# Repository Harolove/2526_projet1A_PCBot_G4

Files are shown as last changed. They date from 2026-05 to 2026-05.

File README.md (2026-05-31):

# 2526_projet1A_PCBot_G4
PCBot fait par le groupe de 4

## Rappels git

### Clé SSH

Dans git bash, lancez la commande suivante :

```bash
ssh-keygen
```

puis affichez la clé :

```bash
cat /c/Users/<USER>/.ssh/id_ed25519.pub
```

Créez une nouvelle clé dans github et collez la clé

### Clonez le projet

Pour récupérer le projet, à faire une fois (par projet).

```bash
git clone git@github.com:Harolove/2526_projet1A_PCBot_G4.git
```

### Faire un commit

A faire à chaque fois que quelque chose fonctionne, et après une séance de travail.

```bash
git status
git add .
git commit -m "Message"
git push
```

### Récupérer la dernière version

A faire à chaque fois qu'on commence à travailler

```bash
git pull
```
## Timeline
### 05/02/2026
Début du projet : Le professeur nous présente différents projets.
Nous avons choisi le PCBot car le projet nous paraît très intéressant même s'il en est un gros. Nous avons également utilisé cette séance pour découvrir git et github. Nous avons commencé les recherches des datasheets des différents composants du PCBot; et nous avons listé les différentes fonctionnalités de celui-ci.

### 12/02/2026
Draw.io :
- Schéma architectural

Kicad : 
- Début du schematic
- Modification des symboles déjà existants sur Kicad pour avoir des composants qui se rapprochent de ceux que nous allons utiliser

### 19/02/2026
Kicad :
- Création des feuilles hiérarchiques
- Continuation du schematic sur Kicad

### 12/03/2026
Kicad :
- Continuation du schematic sur Kicad

### 19/03/2026
Kicad : 
- Ajout de connexions inter-feuille
CubeIDE : 
- Début de code (détermination de position, calcul de distance avec obstacle, déplacement dans l'espace)

### 25/03/2026
Kicad :
- Début du routage (ajout des Mounting_Hole_Pad)
- Ajout des plans de masse (GND pour couches n°1, 2 et 4)

### 26/03/2026
CubeIDE :
- Modification du code et ajout de code test (car nous n'avons pas encore la carte)

### 09/04/2026
CubeIDE :
- Correction d'erreurs

### 16/04/2026
CubeIDE :
- Commentaire des différents fichiers .c et .h
- Recherche d'une librairie pour le capteur TOF

### 06/05/2026
Software : 
- Réussite à faire communiquer deux nRF24 avec deux Nucléos-L476RG

### 07/05/2026
Pratique :
- Soudure du PCB
Software :
- Test du code pour la centrale inertielle

### 13/05/2026
Pratique :
- Resoudure du PCB (car nous avons eu des problèmes la première fois)

### 15/05/2026
Software :
- Fonctionnement de la centrale inertielle

### 18/05/2026
Software :
- Test du code pour le capteur tof (mais n'a pas réussi à le faire fonctionner)
Onshape :
- Modélisation d'un support pour le PCB

### 19/05/2026
Onshape :
- Impression et assemblage du support

### Introduction:

Ce projet a pour objectif la conception d'un robot PCBot capable de connaître sa position dans l'espace et de se déplacer de manière autonome. Ce robot doit pouvoir cartographier un environnement en mesurant la distance qui le sépare des obstacles, et en communiquant avec d'autres PCBot, il peut reconstruire la carte d'un environnement beaucoup plus large.

### Choix des composants:

Nous avons choisi nos composants par rapport à trois critères: l'écologie, l'optimisation de l'espace et le coût.
- Pour la gestion de l'énergie, nous avons retenu le BMS BQ25896RTWR, qui accepte une large plage de tension d'entrée (3,9V à 14V) et offre un rendement supérieur à 90% à 3A, permettant l'utilisation d'adaptateurs standards (5V) ou haute tension (9V/12V).
- Pour le contrôle des moteurs DFR1224 à courant continu, nous avons opté pour le driver DRV8411APWPR pour sa compacité et sa simplicité d'utilisation, avec une large plage de fonctionnement de 1.65V à 11V.
- La localisation du robot repose sur la centrale inertielle LSM6DSOX, qui possède un accéléromètre et un gyroscope (que l'on n'utilisera pas dans le projet) dans un boîtier résistant aux chocs mécaniques.
- Pour la mesure de distance, nous avons choisi le capteur TOF VL53L0X pour ses bonnes performances en pleine lumière dans un encombrement réduit. 
- La communication sans fil entre robots est assurée par le module nRF24.

### Routage et conception du PCB:

Pour le routage, nous avons cherché à minimiser les distances entre composants interdépendants, en plaçant notamment les condensateurs de découplage au plus près des composants qu'ils protègent. Le PCB a été optimisé pour atteindre une taille minimale de 5,9 × 6,8 cm pour l'écologie.
Exemple: 



###

### Difficultés rencontrées:
Le soudage des composants a été l'étape la plus délicate du projet, marquée par plusieurs tentatives avant d'obtenir un résultat satisfaisant. Notre premier PCB a été un échec, car après le passage au four, nous avons remarqué que nous n’avons pas retiré la pâte à braser au niveau des trous du connecteur USB-C, rendant ainsi la carte inutilisable. Lors du deuxième essai, de la pâte à braser s’est retirée par inadvertance à certains endroits, compromettant là encore la qualité des soudures.
Sur notre PCB final, le passage au four a provoqué le déplacement de notre BMS et de certains condensateurs. De plus, une patte de la STM32 s’est pliée rompant ainsi le contact électrique avec plusieurs broches du microcontrôleur. Pour corriger ces problèmes, nous avons dû dessouder les composants concernés et les ressouder manuellement à l'air chaud avec du flux un liquide qui permet à l'étain de couler jusqu'aux pattes lors du chauffage à l'air chaud. Malgré ces difficultés, cette expérience nous a appris énormément sur les contraintes du soudage en production et sur les techniques de reprise manuelle. 

Après le soudage, nous avons tenté d'alimenter le PCB via un chargeur USB-C, mais les tensions mesurées au multimètre ne correspondaient pas aux valeurs attendues. Nous avons découvert que deux solder jumpers, JP1 et JP2, étaient ouverts par défaut, nous avons donc dû poser de l'étain dessus pour enfin avoir des alimentations correctes. Nous avons également constaté que le PCB ne fonctionnait qu'avec un chargeur USB-A, le chargeur USB-C ne semblant pas être reconnu correctement, sans que nous ayons pu en identifier la cause précise.

Du côté logiciel, nous n'avons pas réussi à établir la communication I2C avec le capteur TOF, que ce soit sur le PCB du projet ou avec notre STM32L476RG. Pourtant, la broche XSHUT a bien été mise à 1 dans le code, et l'alimentation du composant a été vérifiée avec un multimètre. 

### Modélisation 3D du support:
Nous avons conçu le support du robot sur OnShape. La principale contrainte de conception était d'assurer que les deux roues arrière et la bille aient la même hauteur pour garantir une surface de contact plane. Nous avons donc ajouté de la matière à l'avant du support afin de compenser la différence de hauteur.
Nous avons fait différents trous pour pouvoir faire rentrer les vis des moteurs et de la bille, et nous avons aussi fait le support pour le PCB. Cependant, l'impression n'a pas été parfaite et le support ne s'est pas emboîté correctement, pour pallier le problème, nous avons cassé l'un des picots du support afin que le PCB puisse tenir en place.





### IMU
Dans le cadre du projet, nous avons réalisé quelques tests avec le composant LSM6DSOX (Adafruit 4438), notre objectif était de pouvoir obtenir la distance parcourue par le composant à partir des données accélérométriques (par double intégration). Nous avons relié les lignes SDA et SCL de l’imu sur les broches PB6 et PB7 du microcontrôleur STM32L476RG.
Avant de faire ces tests, nous avons utilisé le registre WHO_AM_I du composant d’adresse 0x0F et qui contient 0x6C (108). Après lecture du contenu à cette adresse nous avons obtenu cette valeur, cela montre que le capteur est bien connecté.
Les registres OUTX et OUTY permettent de mesurer l'accélération selon l’axe x et l’axe y, cependant, dans le cadre de ces tests, nous allons plutôt nous concentrer sur un seul axe.
L'accélération est codée sur 16 bits au total, mais le bus I2C ne peut transférer que 8 bits à la fois. Donc le capteur découpe la valeur en deux morceaux de 8 bits et les range dans deux registres séparés :
- OUTX_L_A (0x28) contient les 8 bits de poids faible
- OUTX_H_A (0x29) contient les 8 bits de poids fort.



Le registre CTRL1_XL d’adresse 0x10 est le registre de configuration principal de l'accéléromètre. Il est composé de 8 bits répartis en trois parties :
- Les 4 bits de poids fort (ODR_XL3 à ODR_XL0) règlent la fréquence de mesure
- Les 2 bits suivants (FS1_XL, FS0_XL) règlent la plage de mesure
- Le bit LPF2_XL_EN active ou non un filtre passe-bas





Pour nos tests nous avons choisi d’envoyer 0x40 à ce registre qui correspond en binaire à 0100 0000, on a donc :
- 0100 pour ODR_XL qui correspond à 104 Hz dans le tableau pour un mode normal
- 00 pour FS_XL qui correspond à la plage ±2g (valeur par défaut)
- 00 pour le reste: filtre désactivé

On fixe la fréquence d'échantillonnage du capteur à 104 Hz, ce qui signifie qu'il prend 104 mesures par seconde, ce qui est largement suffisant pour nos tests, puisque dt = 0.02s correspond à une fréquence de 50 Hz dans le code. Le capteur mesure donc deux fois plus vite que notre boucle de calcul.
On fixe la plage à ±2g qui est adaptée pour nos tests car nos déplacements sont lents et à faible accélération.

L'approche que nous avons opté pour le code est d’implanter plusieurs variables volatiles:

- measurement_active: cette variable vaut 1 si la mesure est active et 0 sinon.
- pos_x: la position de x actuelle.
- x_pos_max: la position maximale de pox_x pendant une mesure, elle a été introduite car pos_x varie en continu et ne permet pas de lire directement une valeur stable.
  
Une mesure est lancée dès que l’on appuie sur le bouton poussoir PC13 et s’arrête lorsqu’on réappuie dessus pour nous donner la valeur de x_pos_max au cours de cette mesure. 

L'estimation de la position repose sur une double intégration temporelle. Cependant, cette intégration pose un problème de précision, de petites erreurs s'accumulent à chaque intégration et fausse le calcul de la position même quand le robot est immobile. Ainsi, pour limiter ces erreurs, nous avons mis en place 2 corrections:
- Les valeurs brutes du capteur sont converties en m/s² selon la plage de mesure ±2g.
- Si l'accélération est inférieure à 0,20 m/s², on la considère comme du bruit et on l'ignore.

Après implémentation de ce code, nous avons lancé le débogueur et regardé les valeurs de pos_x, x_pos_max et measurement_active dans Live Expressions de l'IDE, permettant d'observer en temps réel ces variables. 
Pour vérifier si notre code fonctionne, nous avons choisi de faire déplacer le capteur de 10 cm, après plusieurs essais, nous obtenons des résultats entre 9.1 et 10.5 cm, ce qui est plutôt satisfaisant.

Voici ce qu'on observe :

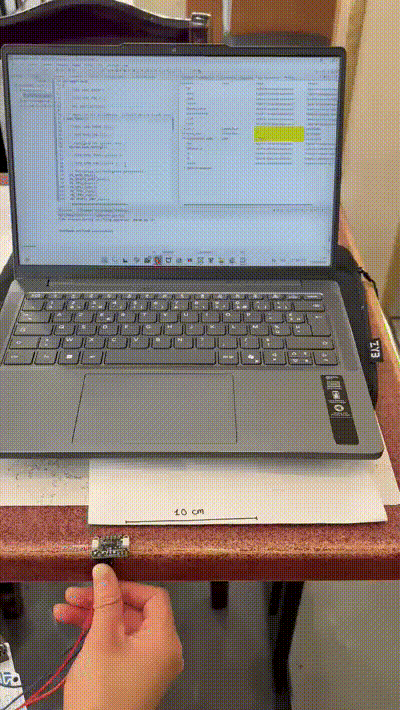
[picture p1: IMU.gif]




### nRF24:

Pour ce projet, nous avons besoin de faire communiquer deux robots distants.
Les capteurs LiDAR permettent une mesure précise, mais leur coût élevé et leur complexité de mise en œuvre (drivers, protocoles temps réel) dépassent les contraintes du projet. Nous avons donc opté pour une communication radio bas-coût avec le module nRF24L01+, qui offre une liaison sans fil simple à intégrer via SPI et suffisamment fiable pour nos besoins.
Nous avons relié deux modules nRF24L01+ à deux cartes Nucleo-L476RG et vérifié que les deux microcontrôleurs pouvaient s'échanger des messages de manière bidirectionnelle :

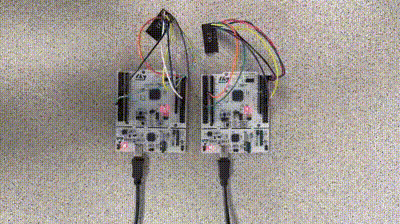
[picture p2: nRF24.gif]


## Connexion matérielle:
Le nRF24L01+ communique via le bus SPI. Voici le câblage utilisé sur le STM32L476RG :
-	CE → PA8 (contrôle émission/réception)
-	CSN → PB6 (Chip Select SPI)
-	SCK → PA5 (SPI1_SCK)
-	MOSI → PA7 (SPI1_MOSI)
-	MISO → PA6 (SPI1_MISO)
-	VCC → 3.3 V  |  GND → GND

## Configuration du module:
Les principaux paramètres configurés dans nos tests :
-	Canal RF : canal 76, libre des perturbations Wi-Fi les plus courantes.
-	Débit : 1 Mbps — bon compromis portée/fiabilité pour notre usage.
-	Puissance d'émission : 0 dBm (niveau max), pour assurer la fiabilité en intérieur.
-	Taille de payload : 32 octets (mode statique).
-	Adresses : une adresse TX et une adresse RX configurées de façon symétrique sur les deux cartes.

La validation de la connexion SPI a été réalisée en lisant le registre CONFIG (adresse 0x00) : si la valeur retournée est cohérente (typiquement 0x08 après reset), le module est bien connecté et répond correctement.

## Approche logicielle:
Nous avons distingué deux rôles : un émetteur (TX) et un récepteur (RX), chacun configuré sur une Nucleo. Les fonctions principales sont :
-	nrf24_init() : initialise le SPI et configure les registres (canal, débit, adresses, taille payload).
-	nrf24_send(data, len) : place le module en mode TX, envoie le payload, attend l'acquittement (Auto-ACK).
-	nrf24_receive(buf) : place le module en mode RX, poll le registre STATUS pour détecter une donnée disponible, puis lit le FIFO.

Le bouton poussoir PC13 de la carte émettrice déclenche l'envoi d'un message. La carte réceptrice allume une LED (PA5) à chaque réception confirmée, permettant une vérification visuelle sans débogueur.

## Résultats:
Les tests montrent une communication stable entre les deux cartes.

### Conclusion:
À la fin du projet, nous avons réussi à faire communiquer deux nRF24 entre eux, la centrale inertielle a part et à faire fonctionner les 2 moteurs de roue, donc le robot peut se déplacer mais il ne peut pas encore s'arrêter librement ni changer de vitesse; les 2 LEDs fonctionnent, si D1 celà signifie que le PCB est alimenté et si D2 clignote c'est qu'il y a une erreur au niveau de la batterie (qui n'est pas connectée).

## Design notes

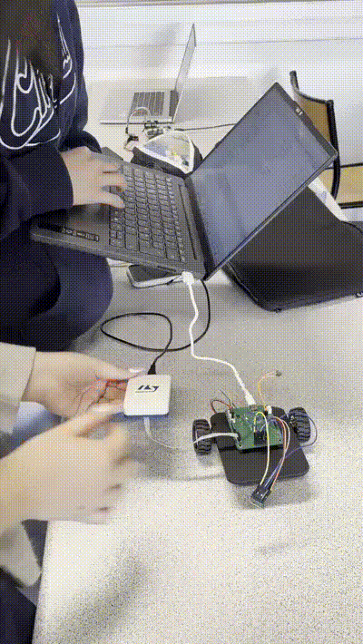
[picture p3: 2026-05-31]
Robot_en_marche.gif

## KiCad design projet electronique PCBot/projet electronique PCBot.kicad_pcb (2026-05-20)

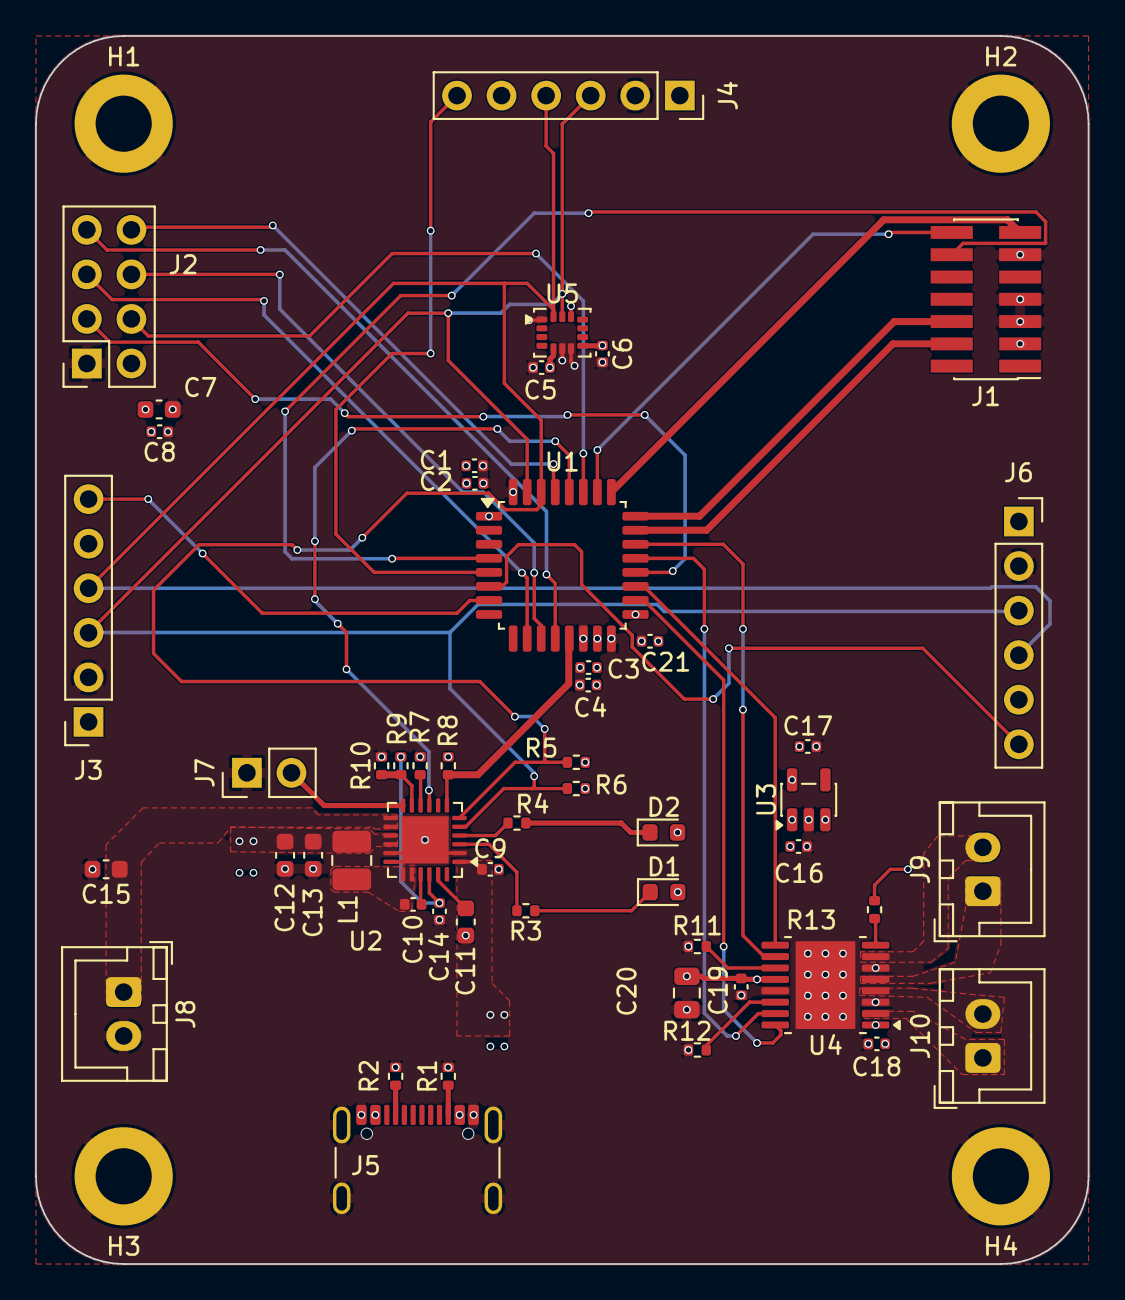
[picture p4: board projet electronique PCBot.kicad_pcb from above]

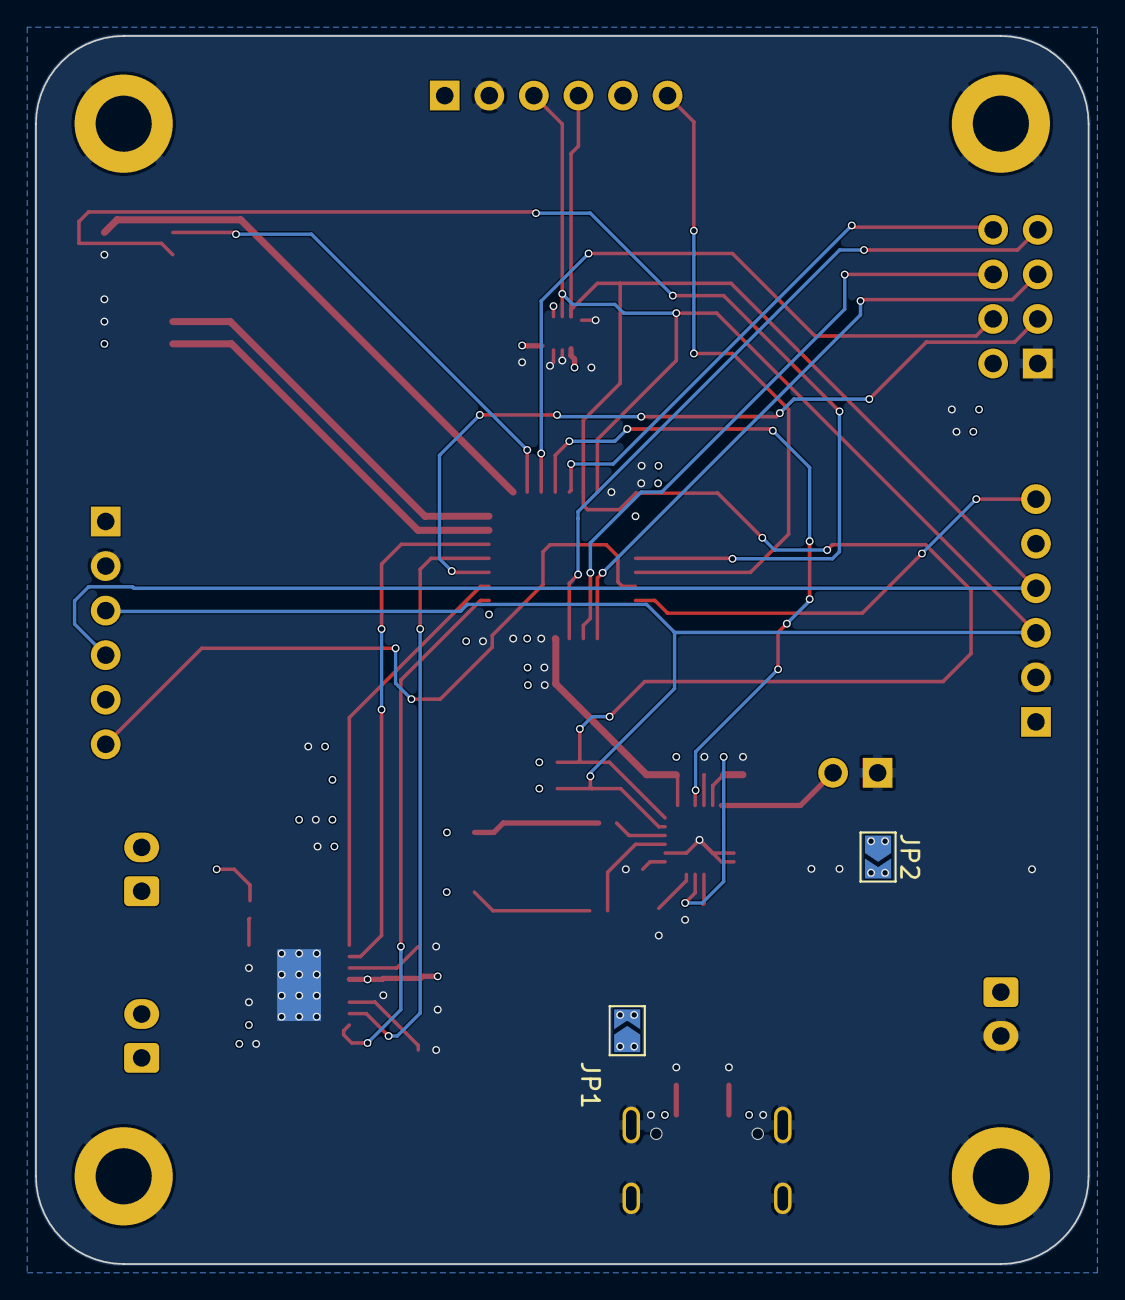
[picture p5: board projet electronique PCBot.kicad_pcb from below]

Board: 4 copper layers, 60.0 x 70.0 mm, 58 parts (2 on the bottom side), 49 nets.

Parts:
C1: 4.7u; C_0402_1005Metric
C2, C5, C6, C8, C18, C19, C21: 100n; C_0402_1005Metric
C3: 10n; C_0402_1005Metric
C4, C9, C16, C17: 1u; C_0402_1005Metric
C7, C12, C13, C15: 10u; C_0603_1608Metric
C10: 47n; C_0402_1005Metric
C11: 8u2; C_0603_1608Metric
C14: 4u7; C_0402_1005Metric
C20: 47u; C_0805_2012Metric
D1, D2: LED; LED_0603_1608Metric
H1, H2, H3, H4: MountingHole_Pad; MountingHole_3.2mm_M3_DIN965_Pad
J1: Conn_ST_STDC14; PinHeader_2x07_P1.27mm_Vertical_SMD
J2: nRF24; PinSocket_2x04_P2.54mm_Vertical
J3, J4, J6: TOF; PinSocket_1x06_P2.54mm_Vertical
J5: USB_C_Receptacle_USB2.0_16P; USB_C_Receptacle_GCT_USB4105-xx-A_16P_TopMnt_Horizontal
J7: ON SWITCH; PinHeader_1x02_P2.54mm_Vertical
J8, J9, J10: Conn_01x02_Pin; JST_XH_B2B-XH-A_1x02_P2.50mm_Vertical
JP1, JP2: SolderJumper_2_Open; SolderJumper-2_P1.3mm_Open_TrianglePad1.0x1.5mm
L1: 1u; L_1008_2520Metric
R1, R2: 5k1; R_0402_1005Metric
R3, R4: 1k; R_0402_1005Metric
R5, R6, R8, R9, R10, R11, R12, R13: 10k; R_0402_1005Metric
R7: 270R; R_0402_1005Metric
U1: STM32G431KBT6; LQFP-32_7x7mm_P0.8mm
U2: BQ25896RTWR; Texas_RTW_WQFN-24-1EP_4x4mm_P0.5mm_EP2.7x2.7mm
U3: BU33SD5WG-TR; SOT-23-5
U4: DRV8411APWPR; HTSSOP-16-1EP_4.4x5mm_P0.65mm_EP3.4x5mm_Mask2.46x2.31mm_The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
U5: LSM6DSOX; LGA-14_3x2.5mm_P0.5mm_LayoutBorder3x4y

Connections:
+3.3V: C1.1, C2.1, C3.1, C4.1, C5.2, C6.1, C7.1, C8.1, C17.1, C18.2, C21.1, J1.3 (VCC), J2.2, J3.1 (3.3V), J4.1 (3.3V), J6.1 (3.3V), R5.1, R6.1, R8.1, R13.1, U1.1 (VDD), U1.15 (VDDA), U1.17 (VDD), U3.5 (VOUT), U4.1 (VREF), U5.5 (VDDIO), U5.8 (VDD), U5.12 (CS)
/Capteur/CE: J2.3, U1.20 (PA10)
/Capteur/CSN: J2.4, U1.27 (PB4)
/Capteur/IRQ: J2.8, U1.29 (PB6)
/Capteur/MISO: J2.7, U1.12 (PA7)
/Capteur/MOSI: J2.6, U1.11 (PA6)
/Capteur/SCK: J2.5, U1.10 (PA5)
/Capteur/SCL: J3.3 (SCL), J4.3 (SCL), J6.3 (SCL), R6.2, U1.31 (PB8), U2.5 (SCL), U5.13 (SCL)
/Capteur/SDA: J3.4 (SDA), J4.4 (SDA), J6.4 (SDA), R5.2, U1.30 (PB7), U2.6 (SDA), U5.14 (SDA)
/Capteur/TOF1_XSHUT: J3.6 (XST), U1.7 (PA2)
/Capteur/TOF2_XSHUT: J6.6 (XST), U1.6 (PA1)
/Capteur/TOF3_XSHUT: J4.6 (XST), U1.5 (PA0)
/Driver/AOUT1: J10.1, U4.2 (AOUT1)
/Driver/AOUT2: J10.2, U4.4 (AOUT2)
/Driver/BOUT1: J9.2, U4.7 (BOUT1)
/Driver/BOUT2: J9.1, U4.5 (BOUT2)
/Driver/TIM1_CH1: U1.18 (PA8), U4.16 (AIN1)
/Driver/TIM1_CH1N: U1.21 (PA11), U4.15 (AIN2)
/Driver/TIM1_CH2: U1.19 (PA9), U4.9 (BIN1)
/Driver/TIM1_CH2N: U1.22 (PA12), U4.10 (BIN2)
/Driver/nFAULT: R13.2, U4.8 (nFAULT)
/Gestion d'energie/INT: R8.2, U1.13 (PB0), U2.7 (INT)
/Gestion d'energie/SW: C10.1, L1.1, U2.19 (SW), U2.20 (SW)
/Gestion d'energie/SYS: C16.1, C19.1, C20.1, D1.2 (A), D2.2 (A), JP2.2 (B), U3.1 (VIN), U3.3 (~SHDN), U4.12 (VM)
/Gestion d'energie/VBUS: J5.A4 (VBUS), J5.A9 (VBUS), J5.B4 (VBUS), J5.B9 (VBUS), JP1.1 (A)
/Gestion d'energie/VBUS_TO_BQ: C9.1, JP1.2 (B), U2.1 (VBUS)
/Gestion d'energie/~CE: U1.28 (PB5), U2.9 (~CE)
/STM32/NRST: J1.12 (~RST), U1.4 (PG10)
/STM32/SYS_JTCK-SWCLK: J1.6 (JCLK/SWCLK), U1.24 (PA14)
/STM32/SYS_JTMS-SWDIO: J1.4 (JTMS/SWDIO), U1.23 (PA13)
/STM32/USART2_RX: J1.13 (VCP_RX), U1.25 (PA15)
/STM32/USART2_TX: J1.14 (VCP_TX), U1.26 (PB3)
GND: C1.2, C2.2, C3.2, C4.2, C5.1, C6.2, C7.2, C8.2, C9.2, C11.1, C12.2, C13.2, C14.2, C15.2, C16.2, C17.2, C18.1, C19.2, C20.2, C21.2, H1.1 (1_1), H2.1 (1_1), H3.1 (1_1), H4.1 (1_1), J1.5 (GND), J1.7 (GND), J1.11 (GNDDetect), J2.1, J3.2 (GND), J4.2 (GND), J5.A1 (GND), J5.A12 (GND), J5.B1 (GND), J5.B12 (GND), J5.S1 (SHIELD), J6.2 (GND), J7.1, J8.2, R1.2, R2.2, R7.1, R10.2, R11.1, R12.1, U1.14 (VSSA), U1.16 (VSS), U1.32 (VSS), U2.2 (PSEL), U2.17 (PGND), U2.18 (PGND), U2.25 (PGND), U3.2 (GND), U4.3 (PGNDA), U4.6 (PGNDB), U4.13 (GND), U4.17 (GND(PPAD)), U5.1 (SDO/SA0), U5.6 (GND), U5.7 (GND)
unnamed: D1.1 (K), R3.1
unnamed: D2.1 (K), R4.2
unnamed: J5.A5 (CC1), R2.1
unnamed: J5.B5 (CC2), R1.1
unnamed: J7.2, U2.12 (~QON)
unnamed: C15.1, J8.1, U2.13 (BAT), U2.14 (BAT)
unnamed: C12.1, C13.1, JP2.1 (A), L1.2, U2.15 (SYS), U2.16 (SYS)
unnamed: C10.2, U2.21 (BTST)
unnamed: R7.2, U2.10 (ILIM)
unnamed: C11.2, U2.23 (PMID)
unnamed: C14.1, R9.1, U2.22 (REGN)
unnamed: R4.1, U2.4 (STAT)
unnamed: R9.2, R10.1, U2.11 (TS)
unnamed: R3.2, U2.3 (~PG)
unnamed: R12.2, U4.14 (AIPROPI)
unnamed: R11.2, U4.11 (BIPROPI)

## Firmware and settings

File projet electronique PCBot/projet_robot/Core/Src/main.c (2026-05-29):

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

#include "main.h"

/* USER CODE BEGIN Includes */
#include "odometrie.h"
#include "moteur.h"
#include "capteur.h"
#include "comm.h"
#include "imu.h"
#include "map.h"
#include "zone.h"
#include <stdint.h>

/* USER CODE END Includes */

I2C_HandleTypeDef hi2c1;
TIM_HandleTypeDef htim1;

/* USER CODE BEGIN PV */
TIM_HandleTypeDef htim2;
TIM_HandleTypeDef htim3;
TIM_HandleTypeDef htim4;
TIM_HandleTypeDef htim6;
volatile uint16_t raw = 0;
volatile float distance_cm = 0;
/* USER CODE END PV */

UART_HandleTypeDef huart2;

/* USER CODE BEGIN PV 2 */
RobotPose maPosition;
Moteur mot_gauche, mot_droit;

#define SPEED_SLOW           20
#define SPEED_NORMAL         20
#define SPEED_RECUL          15
#define SPEED_PIVOT          18
#define OBSTACLE_DISTANCE_CM 20.0f
#define BACKUP_TIME_MS       600
#define TURN_TIME_MS         500
#define CONTROL_LOOP_MS      50

MapGrid  global_map;
Zone     my_zone;
CAPTEUR_t monCapteur;
/* USER CODE END PV 2 */

void SystemClock_Config(void);
static void MX_GPIO_Init(void);
static void MX_I2C1_Init(void);
static void MX_TIM1_Init(void);
static void MX_USART2_UART_Init(void);

/* USER CODE BEGIN PFP */
static void Robot_Stop(void);
static void Robot_SetSpeeds(int32_t left, int32_t right);
static int32_t Robot_ClampSpeed(int32_t speed);
static void Robot_AvoidObstacle(void);
static void Robot_RunStep(void);
static void MX_TIM2_Init(void);
static void MX_TIM3_Init(void);
static void MX_TIM4_Init(void);
static void MX_TIM6_Init(void);
/* USER CODE END PFP */

/* USER CODE BEGIN 0 */
static void Robot_SetSpeeds(int32_t left, int32_t right) {
    MOTEUR_SetVitesse(&mot_gauche, left);
    MOTEUR_SetVitesse(&mot_droit,  right);
}

static void Robot_Stop(void) {
    MOTEUR_SetVitesse(&mot_gauche, 0);
    MOTEUR_SetVitesse(&mot_droit,  0);
}


static int32_t Robot_ClampSpeed(int32_t speed) {
    if (speed > 100) return 100;
    if (speed < -100) return -100;
    return speed;
}

static void Robot_AvoidObstacle(void) {
    /* 1. Stop net */
    Robot_Stop();
    HAL_Delay(100);

    /* 2. Recule lent */
    Robot_SetSpeeds(-SPEED_RECUL, -SPEED_RECUL);
    HAL_Delay(BACKUP_TIME_MS);
    Robot_Stop();
    HAL_Delay(100);

    /* 3. Pivot lent sur place (tourne à gauche) */
    Robot_SetSpeeds(-SPEED_PIVOT, SPEED_PIVOT);
    HAL_Delay(TURN_TIME_MS);
    Robot_Stop();
}


static void Robot_RunStep(void) {
    int32_t left_speed;
    int32_t right_speed;
    ODOM_Update(&maPosition, &htim2, &htim3);
    raw = CAPTEUR_Read_Distance(&hi2c1,0x2A);
    distance_cm = (float)raw / 10.0f;
    if (raw != 9999 && raw != 2001 && distance_cm < 150.0f) {
        float obs_x = maPosition.x + (distance_cm / 100.0f) * cosf(maPosition.theta);
        float obs_y = maPosition.y + (distance_cm / 100.0f) * sinf(maPosition.theta);
        MAP_AddObstacle(&global_map, obs_x, obs_y);
    }

    if (raw == 9999) { //test I2C
        Robot_Stop();
    } else if (raw == 2001) {
        Robot_SetSpeeds(SPEED_NORMAL, SPEED_NORMAL);
    } else if (distance_cm <= OBSTACLE_DISTANCE_CM) {
        Robot_AvoidObstacle();
    } else {
        Robot_SetSpeeds(SPEED_NORMAL, SPEED_NORMAL);
    }

    COMM_SendToBase(&maPosition, distance_cm);
    HAL_Delay(CONTROL_LOOP_MS);
}

/* USER CODE END 0 */

int main(void)
{
    HAL_Init();
    SystemClock_Config();

    MX_GPIO_Init();
    MX_I2C1_Init();
    MX_TIM1_Init();
    MX_USART2_UART_Init();

    /* USER CODE BEGIN 2
    HAL_GPIO_WritePin(GPIOA, GPIO_PIN_0 | GPIO_PIN_1 | GPIO_PIN_2, GPIO_PIN_RESET);
    HAL_Delay(10);

   // TOF 1 ùmilieu
    HAL_GPIO_WritePin(GPIOA, GPIO_PIN_0, GPIO_PIN_SET); // Allume TOF1
    HAL_Delay(2);
    Capteur_SetAddress(&hi2c1, 0x29, 0x2A); // Change 0x29 (adresse 7-bit par défaut) vers 0x2A

    // TOF 2 centre
    HAL_GPIO_WritePin(GPIOA, GPIO_PIN_1, GPIO_PIN_SET); // Allume TOF2
    HAL_Delay(2);
    Capteur_SetAddress(&hi2c1, 0x29, 0x2B); // Change 0x29 vers 0x2B

    // TOF 3 droite
    HAL_GPIO_WritePin(GPIOA, GPIO_PIN_2, GPIO_PIN_SET); // Allume TOF3
    HAL_Delay(2);

    Capteur_SetAddress(&hi2c1, 0x29, 0x2C);
    */

    MX_TIM2_Init();
    MX_TIM3_Init();
    MX_TIM4_Init();
    MX_TIM6_Init();


    //Initialisation odométrie
    ODOM_Init(&maPosition);
    maPosition.id = 1;

    //Démarrage des encodeurs
    HAL_TIM_Encoder_Start(&htim2, TIM_CHANNEL_ALL);
    HAL_TIM_Encoder_Start(&htim3, TIM_CHANNEL_ALL);

    // Initialisation des modules
    MAP_Init(&global_map);
    ZONE_AssignFromID(maPosition.id, &my_zone);
    COMM_Init(&huart2);

    // Configuration moteur gauche — TIM1 CH1 (PA8) et CH1N (PA11)
    mot_gauche.htim    = &htim1;
    mot_gauche.channel = TIM_CHANNEL_1;
    MOTEUR_Init(&mot_gauche);

    // Configuration moteur droit — TIM1 CH2 (PA9) et CH2N (PA12)
    mot_droit.htim    = &htim1;
    mot_droit.channel = TIM_CHANNEL_2;
    MOTEUR_Init(&mot_droit);



    //Démarrage PWM TIM1
    HAL_TIM_PWM_Start(&htim1,   TIM_CHANNEL_1);
    HAL_TIMEx_PWMN_Start(&htim1, TIM_CHANNEL_1);
    HAL_TIM_PWM_Start(&htim1,   TIM_CHANNEL_2);
    HAL_TIMEx_PWMN_Start(&htim1, TIM_CHANNEL_2);


    /* USER CODE END 2 */
    while (1)
    {
        Robot_SetSpeeds(20, 20);
        /*HAL_Delay(5000); // 5 secondes*/

        // Phase 2 10 cm/s pendant 5 secondes
        Robot_SetSpeeds(10, 10);
        /*HAL_Delay(5000);*/

        // 3. Phase 3 arret
        Robot_Stop();
        /*HAL_Delay(5000);*/
/*
    	uint8_t imu_id = IMU_Check(&hi2c1);
    	if (imu_id == 0x6C) {
    	    //si entre ici, imu détecté
    	    HAL_GPIO_WritePin(GPIOA, GPIO_PIN_5, 1);
    	} else {
    	    // Si imu_id vaut 0, le bus est toujours bloqué ou l'adresse est 0x6B!
    	}
    	raw = CAPTEUR_Read_Distance(&hi2c1, 0x2A);// capteur milieu
    	    if (raw < 2000) {
    	      // si entre ici ça marche
    	    }

    	    HAL_Delay(50);
    	   */
// Robot_RunStep ();
    }
}

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
/* USER CODE BEGIN 4 */

static void MX_TIM2_Init(void)
{
    TIM_Encoder_InitTypeDef sConfig      = {0};
    TIM_MasterConfigTypeDef sMasterConfig = {0};

    __HAL_RCC_TIM2_CLK_ENABLE();

    htim2.Instance               = TIM2;
    htim2.Init.Prescaler         = 0;
    htim2.Init.CounterMode       = TIM_COUNTERMODE_UP;
    htim2.Init.Period            = 65535;
    htim2.Init.ClockDivision     = TIM_CLOCKDIVISION_DIV1;
    htim2.Init.AutoReloadPreload = TIM_AUTORELOAD_PRELOAD_DISABLE;

    sConfig.EncoderMode   = TIM_ENCODERMODE_TI12;
    sConfig.IC1Polarity   = TIM_ICPOLARITY_RISING;
    sConfig.IC1Selection  = TIM_ICSELECTION_DIRECTTI;
    sConfig.IC1Prescaler  = TIM_ICPSC_DIV1;
    sConfig.IC1Filter     = 0;
    sConfig.IC2Polarity   = TIM_ICPOLARITY_RISING;
    sConfig.IC2Selection  = TIM_ICSELECTION_DIRECTTI;
    sConfig.IC2Prescaler  = TIM_ICPSC_DIV1;
    sConfig.IC2Filter     = 0;

    if (HAL_TIM_Encoder_Init(&htim2, &sConfig) != HAL_OK) Error_Handler();

    sMasterConfig.MasterOutputTrigger = TIM_TRGO_RESET;
    sMasterConfig.MasterSlaveMode     = TIM_MASTERSLAVEMODE_DISABLE;
    if (HAL_TIMEx_MasterConfigSynchronization(&htim2, &sMasterConfig) != HAL_OK) Error_Handler();
}

static void MX_TIM3_Init(void)
{
    TIM_Encoder_InitTypeDef sConfig      = {0};
    TIM_MasterConfigTypeDef sMasterConfig = {0};

    __HAL_RCC_TIM3_CLK_ENABLE();

    htim3.Instance               = TIM3;
    htim3.Init.Prescaler         = 0;
    htim3.Init.CounterMode       = TIM_COUNTERMODE_UP;
    htim3.Init.Period            = 65535;
    htim3.Init.ClockDivision     = TIM_CLOCKDIVISION_DIV1;
    htim3.Init.AutoReloadPreload = TIM_AUTORELOAD_PRELOAD_DISABLE;

    sConfig.EncoderMode   = TIM_ENCODERMODE_TI12;
    sConfig.IC1Polarity   = TIM_ICPOLARITY_RISING;
    sConfig.IC1Selection  = TIM_ICSELECTION_DIRECTTI;
    sConfig.IC1Prescaler  = TIM_ICPSC_DIV1;
    sConfig.IC1Filter     = 0;
    sConfig.IC2Polarity   = TIM_ICPOLARITY_RISING;
    sConfig.IC2Selection  = TIM_ICSELECTION_DIRECTTI;
    sConfig.IC2Prescaler  = TIM_ICPSC_DIV1;
    sConfig.IC2Filter     = 0;

    if (HAL_TIM_Encoder_Init(&htim3, &sConfig) != HAL_OK) Error_Handler();

    sMasterConfig.MasterOutputTrigger = TIM_TRGO_RESET;
    sMasterConfig.MasterSlaveMode     = TIM_MASTERSLAVEMODE_DISABLE;
    if (HAL_TIMEx_MasterConfigSynchronization(&htim3, &sMasterConfig) != HAL_OK) Error_Handler();
}

static void MX_TIM4_Init(void)
{
    TIM_OC_InitTypeDef      sConfigOC    = {0};
    TIM_MasterConfigTypeDef sMasterConfig = {0};

    __HAL_RCC_TIM4_CLK_ENABLE();

    htim4.Instance               = TIM4;
    htim4.Init.Prescaler         = 159;
    htim4.Init.CounterMode       = TIM_COUNTERMODE_UP;
    htim4.Init.Period            = 999;
    htim4.Init.ClockDivision     = TIM_CLOCKDIVISION_DIV1;
    htim4.Init.AutoReloadPreload = TIM_AUTORELOAD_PRELOAD_DISABLE;

    if (HAL_TIM_PWM_Init(&htim4) != HAL_OK) Error_Handler();

    sMasterConfig.MasterOutputTrigger = TIM_TRGO_RESET;
    sMasterConfig.MasterSlaveMode     = TIM_MASTERSLAVEMODE_DISABLE;
    if (HAL_TIMEx_MasterConfigSynchronization(&htim4, &sMasterConfig) != HAL_OK) Error_Handler();

    sConfigOC.OCMode     = TIM_OCMODE_PWM1;
    sConfigOC.Pulse      = 0;
    sConfigOC.OCPolarity = TIM_OCPOLARITY_HIGH;
    sConfigOC.OCFastMode = TIM_OCFAST_DISABLE;

    if (HAL_TIM_PWM_ConfigChannel(&htim4, &sConfigOC, TIM_CHANNEL_1) != HAL_OK) Error_Handler();
    if (HAL_TIM_PWM_ConfigChannel(&htim4, &sConfigOC, TIM_CHANNEL_2) != HAL_OK) Error_Handler();
}

static void MX_TIM6_Init(void)
{
    TIM_MasterConfigTypeDef sMasterConfig = {0};

    __HAL_RCC_TIM6_CLK_ENABLE();

    htim6.Instance               = TIM6;
    htim6.Init.Prescaler         = 159;
    htim6.Init.CounterMode       = TIM_COUNTERMODE_UP;
    htim6.Init.Period            = 65535;
    htim6.Init.AutoReloadPreload = TIM_AUTORELOAD_PRELOAD_DISABLE;

    if (HAL_TIM_Base_Init(&htim6) != HAL_OK) Error_Handler();

    sMasterConfig.MasterOutputTrigger = TIM_TRGO_RESET;
    sMasterConfig.MasterSlaveMode     = TIM_MASTERSLAVEMODE_DISABLE;
    if (HAL_TIMEx_MasterConfigSynchronization(&htim6, &sMasterConfig) != HAL_OK) Error_Handler();
}

/* USER CODE END 4 */

void Error_Handler(void)
{
    __disable_irq();
    while (1) {}
}

#ifdef USE_FULL_ASSERT
void assert_failed(uint8_t *file, uint32_t line) {}
#endif

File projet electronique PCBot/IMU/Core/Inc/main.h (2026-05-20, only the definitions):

#define B1_Pin GPIO_PIN_13
#define B1_GPIO_Port GPIOC
#define B1_EXTI_IRQn EXTI15_10_IRQn
#define SPI_CS_Pin GPIO_PIN_0
#define SPI_CS_GPIO_Port GPIOC
#define MAGNETO_STATUS_Pin GPIO_PIN_1
#define MAGNETO_STATUS_GPIO_Port GPIOC
#define USART_TX_Pin GPIO_PIN_2
#define USART_TX_GPIO_Port GPIOA
#define USART_RX_Pin GPIO_PIN_3
#define USART_RX_GPIO_Port GPIOA
#define LD2_Pin GPIO_PIN_5
#define LD2_GPIO_Port GPIOA
#define STEPPER_DIR_Pin GPIO_PIN_7
#define STEPPER_DIR_GPIO_Port GPIOA
#define GPS_PPS_Pin GPIO_PIN_4
#define GPS_PPS_GPIO_Port GPIOC
#define BTN_CENTER_Pin GPIO_PIN_5
#define BTN_CENTER_GPIO_Port GPIOC
#define MAGNETO_INT_Pin GPIO_PIN_0
#define MAGNETO_INT_GPIO_Port GPIOB
#define LED_3_Pin GPIO_PIN_1
#define LED_3_GPIO_Port GPIOB
#define LED_1_Pin GPIO_PIN_2
#define LED_1_GPIO_Port GPIOB
#define BTN_BOTTOM_Pin GPIO_PIN_11
#define BTN_BOTTOM_GPIO_Port GPIOB
#define BTN_BOTTOM_EXTI_IRQn EXTI15_10_IRQn
#define GPS_ENN_Pin GPIO_PIN_13
#define GPS_ENN_GPIO_Port GPIOB
#define LED_6_Pin GPIO_PIN_14
#define LED_6_GPIO_Port GPIOB
#define LED_4_Pin GPIO_PIN_15
#define LED_4_GPIO_Port GPIOB
#define BTN_LEFT_Pin GPIO_PIN_6
#define BTN_LEFT_GPIO_Port GPIOC
#define LED_0_Pin GPIO_PIN_7
#define LED_0_GPIO_Port GPIOC
#define BTN_TOP_Pin GPIO_PIN_8
#define BTN_TOP_GPIO_Port GPIOC
#define BTN_RIGHT_Pin GPIO_PIN_9
#define BTN_RIGHT_GPIO_Port GPIOC
#define LED_2_Pin GPIO_PIN_8
#define LED_2_GPIO_Port GPIOA
#define STEPPER_MS1_Pin GPIO_PIN_11
#define STEPPER_MS1_GPIO_Port GPIOA
#define STEPPER_ENN_Pin GPIO_PIN_12
#define STEPPER_ENN_GPIO_Port GPIOA
#define TMS_Pin GPIO_PIN_13
#define TMS_GPIO_Port GPIOA
#define TCK_Pin GPIO_PIN_14
#define TCK_GPIO_Port GPIOA
#define ENC_BTN_Pin GPIO_PIN_15
#define ENC_BTN_GPIO_Port GPIOA
#define ENC_BTN_EXTI_IRQn EXTI15_10_IRQn
#define LED_5_Pin GPIO_PIN_4
#define LED_5_GPIO_Port GPIOB
#define LED_7_Pin GPIO_PIN_5
#define LED_7_GPIO_Port GPIOB

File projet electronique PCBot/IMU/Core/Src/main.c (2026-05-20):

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
/* Includes ------------------------------------------------------------------*/
#include "main.h"
#include "adc.h"
#include "i2c.h"
#include "spi.h"
#include "tim.h"
#include "usart.h"
#include "gpio.h"

/* USER CODE BEGIN Includes */
#include "IMU.h"
/* USER CODE END Includes */



/* USER CODE BEGIN PV */
volatile float acc_x = 0, vit_x = 0, pos_x = 0;
volatile float x_pos_max = 0;
float dt = 0.02f;

// Nouvelles variables pour la gestion du bouton et de l'état
uint8_t measurement_active = 0; // 0 = Idle, 1 = Mesure en cours
uint8_t last_button_state = GPIO_PIN_RESET;
/* USER CODE END PV */


void SystemClock_Config(void);
/**
  * @brief  The application entry point.
  * @retval int
  */
int main(void)
{

  /* MCU Configuration--------------------------------------------------------*/

  /* Reset of all peripherals, Initializes the Flash interface and the Systick. */
  HAL_Init();

  /* Configure the system clock */
  SystemClock_Config();

  /* Initialize all configured peripherals */
  MX_GPIO_Init();
  MX_USART2_UART_Init();
  MX_I2C1_Init();
  MX_SPI2_Init();
  MX_TIM2_Init();
  MX_TIM3_Init();
  MX_USART1_UART_Init();
  MX_ADC1_Init();
  MX_TIM4_Init();

  /* USER CODE BEGIN 2 */
  if (LSM6D_Init(&hi2c1)) {
  }
    /* USER CODE END 2 */

  /* Infinite loop */
  /* USER CODE BEGIN WHILE */
  while (1)
    {
        // 1. Gestion du bouton bleu (mode Toggle avec détection de front)
        uint8_t current_button_state = HAL_GPIO_ReadPin(GPIOC, GPIO_PIN_13); // Bouton bleu sur PC13

        // Si on appuie sur le bouton (front descendant car Pull-up sur Nucleo)
        // Note : Sur Nucleo, le bouton bleu est à 0 quand on appuie.
        if (current_button_state == GPIO_PIN_RESET && last_button_state == GPIO_PIN_SET) {
            HAL_Delay(50); // Anti-rebond simple

            if (measurement_active == 0) {
                // DÉMARRAGE DE LA MESURE
                vit_x = 0;
                pos_x = 0;
                x_pos_max = 0;
                measurement_active = 1;
                // Optionnel : Envoyer un message UART "Start" ici
            } else {
                // ARRÊT DE LA MESURE
                measurement_active = 0;
                // Ici, x_pos_max reste figé, tu peux le lire tranquillement
            }
        }
        last_button_state = current_button_state;

        // 2. Calculs uniquement si la mesure est active
        if (measurement_active) {
            int16_t x_raw = LSM6D_Read_Accel_X(&hi2c1);

            // Conversion G -> m/s^2 (Sensibilité 2G par défaut = 16384 LSB/g)
            acc_x = ((float)x_raw / 16384.0f) * 9.81f;

            // Seuil de bruit (Deadzone) pour éviter la dérive à l'arrêt
            if (acc_x < 0.20f && acc_x > -0.20f) acc_x = 0;

            // Intégration 1 : Vitesse
            vit_x = vit_x + (acc_x * dt);

            // Friction pour stabiliser si l'accélération est nulle
            if (acc_x == 0) vit_x *= 0.95f;

            // Intégration 2 : Position
            pos_x = pos_x + (vit_x * dt);

            // Calcul de la distance absolue parcourue
            float abs_pos = (pos_x < 0) ? -pos_x : pos_x;

            // Mise à jour du record
            if (abs_pos > x_pos_max) {
                x_pos_max = abs_pos;
            }
        }

        // 3. Affichage ou Debug (Toutes les 20ms)
        // Tu peux mettre un point d'arrêt ici pour lire x_pos_max dans les variables
        HAL_Delay(20);
    }
  /* USER CODE END 3 */
}

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
/**
  * @brief  Period elapsed callback in non blocking mode
  * @note   This function is called  when TIM6 interrupt took place, inside
  * HAL_TIM_IRQHandler(). It makes a direct call to HAL_IncTick() to increment
  * a global variable "uwTick" used as application time base.
  * @param  htim : TIM handle
  * @retval None
  */
void HAL_TIM_PeriodElapsedCallback(TIM_HandleTypeDef *htim)
{
  if (htim->Instance == TIM6)
  {
    HAL_IncTick();
  }
}

/**
  * @brief  This function is executed in case of error occurrence.
  * @retval None
  */
void Error_Handler(void)
{
  /* USER CODE BEGIN Error_Handler_Debug */
  /* User can add his own implementation to report the HAL error return state */
  __disable_irq();
  while (1)
  {
  }
  /* USER CODE END Error_Handler_Debug */
}
#ifdef USE_FULL_ASSERT
/**
  * @brief  Reports the name of the source file and the source line number
  *         where the assert_param error has occurred.
  * @param  file: pointer to the source file name
  * @param  line: assert_param error line source number
  * @retval None
  */
void assert_failed(uint8_t *file, uint32_t line)
{
  /* USER CODE BEGIN 6 */
  /* User can add his own implementation to report the file name and line number,
     ex: printf("Wrong parameters value: file %s on line %d\r\n", file, line) */
  /* USER CODE END 6 */
}
#endif /* USE_FULL_ASSERT */

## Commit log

2026-02-05 Test de Dignon
2026-02-18 De petites modifications
    [projet electronique PCBot.kicad_sch]
2026-02-19 Ajout feuilles hiérarchiques
    [capteur.kicad_sch, driver.kicad_sch, gestion_energie.kicad_sch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]
2026-02-19 Ajout de la feuille hiérarchique moteur
    [capteur.kicad_sch, gestion_energie.kicad_sch, moteurs.kicad_sch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]
2026-02-19 Modification des feuilles hiérarchiques et le main
    [capteur.kicad_sch, gestion_energie.kicad_sch, projet electronique PCBot.kicad_sch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]
2026-02-19 ajout de la feuille connecteurs
    [capteur.kicad_sch, connecteurs.kicad_sch, driver.kicad_sch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]
2026-02-19 ajout de la feuille usb
    [projet electronique PCBot.kicad_sch, usb.kicad_sch]
2026-02-19 modification de la feuille driver
    [driver.kicad_sch]
2026-02-19 Ajour USB
    [projet electronique PCBot.kicad_sch, usb.kicad_sch]
2026-02-19 modification gestion_energie
    [gestion_energie.kicad_sch]
2026-03-12 feuille driver
    [driver.kicad_sch]
2026-03-12 feuille driver 2
    [driver.kicad_sch, projet electronique PCBot.kicad_sch]
2026-03-12 modification de la feuille capteurs
    [capteur.kicad_sch, stm32.kicad_sch]
2026-03-12 fichier driver et gestion d'energie
    [driver.kicad_sch, gestion_energie.kicad_sch, projet electronique PCBot.kicad_sch]
2026-03-12 re modification de gestion energie
    [gestion_energie.kicad_sch, projet electronique PCBot.kicad_sch, stm32.kicad_sch]
2026-03-18 modifications dans feuilles stm et capteurs
    [capteur.kicad_sch, gestion_energie.kicad_sch, projet electronique PCBot.kicad_sch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]
2026-03-19 modif de flo capteur
    [capteur.kicad_sch]
2026-03-19 modif de capteurs le vrai de vrai
    [capteur.kicad_sch]
2026-03-19 suppression feuilles moteurs et connecteurs + modif feuille stm
    [projet electronique PCBot.kicad_sch, stm32.kicad_sch]
2026-03-19 Ajout du projet STM32CubeIDE pour le robot
2026-03-19 ajout de connexions
    [driver.kicad_sch, gestion_energie.kicad_sch, projet electronique PCBot.kicad_sch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]
2026-03-19 changement de capteur et moteur code
2026-03-19 petites modifications
    [capteur.kicad_sch, driver.kicad_sch, gestion_energie.kicad_sch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]
2026-03-23 modif un lundi lambda
    [driver.kicad_sch, projet electronique PCBot.kicad_sch]
2026-03-23 re modif de lundi
    [projet electronique PCBot.kicad_sch, stm32.kicad_sch]
2026-03-24 grosse modif pcb du prof
    [capteur.kicad_sch, driver.kicad_sch, gestion_energie.kicad_sch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]
2026-03-25 modif après revu prof
    [driver.kicad_sch, projet electronique PCBot.kicad_sch, stm32.kicad_sch]
2026-03-25 début routage
    [projet electronique PCBot.kicad_pcb, projet electronique PCBot.kicad_sch, stm32.kicad_sch]
2026-03-26 placement sur kicad debut
    [projet electronique PCBot.kicad_pcb, stm32.kicad_sch]
2026-03-26 ajout de commentaires et nouveaux fichiers
2026-03-26 suite placement composants
    [driver.kicad_sch, gestion_energie.kicad_sch, projet electronique PCBot.kicad_pcb]
2026-03-26 routage avec bcp d'erreurs
    [projet electronique PCBot.kicad_pcb, projet electronique PCBot.kicad_sch, usb.kicad_sch]
2026-03-26 suite routage
    [projet electronique PCBot.kicad_pcb]
2026-03-26 routage avec 30 erreurs
    [projet electronique PCBot.kicad_pcb]
2026-03-30 modif routage fin
    [driver.kicad_sch, gestion_energie.kicad_sch, projet electronique PCBot.kicad_pcb]
2026-04-02 Dernières corrections LFiack
    [projet electronique PCBot-B_Cu.gbr, projet electronique PCBot-B_Mask.gbr, projet electronique PCBot-B_Paste.gbr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]
2026-04-09 commentaires de code
2026-04-16 modification main map moteur zone à la fin de l'heure
2026-04-16 modification odometrie.c
2026-05-07 début de modification du readme
2026-05-20 modifications code
    [projet electronique PCBot.kicad_pcb]
2026-05-20 nrf24 et imu
2026-05-29 modification finale pour la centrale inertielle

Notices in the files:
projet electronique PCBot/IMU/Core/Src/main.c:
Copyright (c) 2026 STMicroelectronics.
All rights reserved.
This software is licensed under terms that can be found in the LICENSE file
